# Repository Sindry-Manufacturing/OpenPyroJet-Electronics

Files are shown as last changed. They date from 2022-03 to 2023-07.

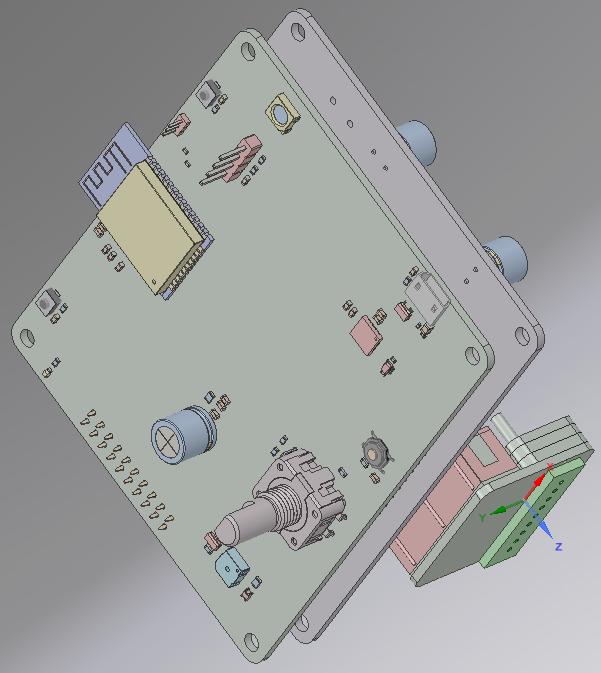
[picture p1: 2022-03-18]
Printhead-Driver/screenshots/3D-PCB-CAD-Model_Controller.jpg

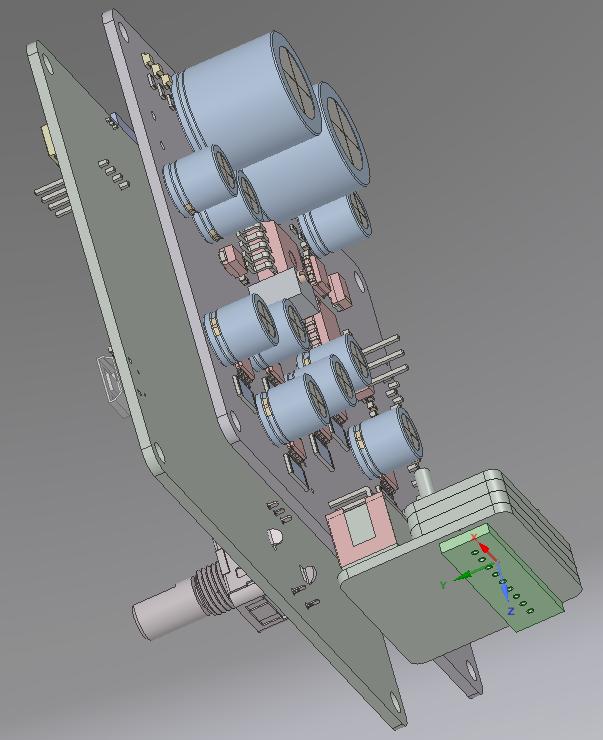
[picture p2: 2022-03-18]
Printhead-Controller/screenshots/3D-PCB-CAD-Model_Driver.jpg

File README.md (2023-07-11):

# OpenPyroJet-Electronics

Software licensed under: AGPL-3

Hardware licensed under: CERN-OHL-S-V2

These sets of sub-folders contain KiCAD 5.1 based designs for experimenting with a PCB based metal/ceramic 3D Printer. 

Gen3.1_Printhead       ; initial experimental PCB based Printhead

Printhead-Controller   ; HW board that runs the Driver board

Printhead-Driver       ; HW circuitry to drive the printhead

software               ; basic Arduino based software to test the Controller & Driver boards.  See: https://github.com/Sindry-Manufacturing/OpenPyrojet-Jetpack  for a much more complete solution

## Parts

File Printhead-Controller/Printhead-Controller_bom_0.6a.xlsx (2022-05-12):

References | Value | Footprint | Quantity Per PCB | Location | LCSC P/N
BZ1 | Buzzer 1KHz - 8KHz | MagneticBuzzer_5.2x5.2_4KHz | 1 | 93-6 | C391030
C2 C3 C5 C6 C7 C8 C9 C10 C12 C14 C15 C18 | 100nF - 6.3V or larger | C_0603_1608Metric | 12 | T15 | C108079
C1 C4 C16 C17 | 10uF - 6.3V or larger | C_0603_1608Metric | 4 | T15 | C326057
C11 | 22uF - 6.3V or larger | C_0603_1608Metric | 1 | T15 | C59461 (https://lcsc.com/product-detail/Multilayer-Ceramic-Capacitors-MLCC-SMD-SMT_Samsung-Electro-Mechanics-CL10A226MQ8NRNC_C59461.html)
C13 - hand solder | 100uF/50V | CP_Radial_D8.0mm_P3.50mm | 1 |  | C365794
D3 | 1N4148 | D_0805_2012Metric | 1 | T9 | C108805
D2 | Green | LED_0603_1608Metric | 1 | T15 | C72043
D4 | PRTR5V0U2X | SOT-143 | 1 | T16 | C316030
D1 | WS2812B | LED_WS2812B_PLCC4_5.0x5.0mm_P3.2mm | 1 | 86-38 | C114586
F1 | 2A Polyfuse | C_0805_2012Metric | 1 | T8 | C2680543 (https://lcsc.com/product-detail/Resettable-Fuses_Jinrui-Electronic-Materials-Co-JK-SMD-0805-200L_C2680543.html)
FB1 | 1uH | R_0805_2012Metric | 1 | T15 | C281114
J5 - hand solder | Conn_02x12_Odd_Even | PinHeader_2x12_P2.54mm_Vertical - Female | 1 | Tray | N/A | https://www.aliexpress.com/item/32747224548.html
J2 | Plug | Hirose_DF13C_CL535-0403-5-51_1x03-1MP_P1.25mm_Vertical | 1 | Tray | N/A* | https://www.aliexpress.com/wholesale?catId=0&initiative_id=SB_20220511181454&SearchText=DF13C-3p+connector
J6 | USB_B_Micro | USB_Micro-B_C319160 | 1 | Table | C319160
Q1 | AO3400A | SOT-23 | 1 | T9 | C344010
R8 | 10 | R_0805_2012Metric | 1 | T2? | C17415
R11 | 47 | R_0603_1608Metric | 1 | T1 | C1211 (https://lcsc.com/product-detail/Chip-span-style-background-color-ff0-Resistor-span-Surface-Mount_UNI-ROYAL-Uniroyal-Elec-0603WAJ0470T5E_C1211.html)
R6 | 2K | R_0603_1608Metric | 1 | T1 | C22975 (https://lcsc.com/product-detail/Chip-span-style-background-color-ff0-Resistor-span-Surface-Mount_UNI-ROYAL-Uniroyal-Elec-0603WAF2001T5E_C22975.html)
R9 R10 | 4.7K | R_0603_1608Metric | 2 | T1 | C23162 (https://lcsc.com/product-detail/Chip-span-style-background-color-ff0-Resistor-span-Surface-Mount_UNI-ROYAL-Uniroyal-Elec-0603WAF4701T5E_C23162.html)
R1 R2 R3 R4 R5 R7 R12 R15 R17 | 10K | R_0603_1608Metric | 9 | T1 | C25804 (https://lcsc.com/product-detail/Chip-span-style-background-color-ff0-Resistor-span-Surface-Mount_UNI-ROYAL-Uniroyal-Elec-0603WAF1002T5E_C25804.html)
R14 | 24K | R_0603_1608Metric | 1 | T1 | C352343 (https://lcsc.com/product-detail/Chip-Resistor-Surface-Mount_Resistor-Today-AECR0603F24K0K9_C352343.html)
R13 | 47K | R_0603_1608Metric | 1 | T1 | C365432 (https://lcsc.com/product-detail/Chip-Resistor-Surface-Mount_Resistor-Today-ETCR0603F47K0K9_C365432.html)
R16 | 1M | R_0603_1608Metric | 1 | T1 | C177633
SW3 | BOOT | SMD_Switch_5x3 | 1 | table | C843665
SW4 | RESET | SMD_Switch_5x3 | 1 | Table | C843665
SW1 | Rotary_Encoder | RotaryEncoder_Alps_EC11E-Switch_Vertical_H20mm | 1 | 93-10 | N/A | https://www.aliexpress.com/item/1744383771.html
SW2 | USER1 | SW_SMD_SPST_SKQG_WithStem_6x6.5 | 1 | table | C318886
U2 | CP2102N-A01-GQFN28 | QFN-28-1EP_5x5mm_P0.5mm_EP3.35x3.35mm | 1 | T12/86-4 | C964632 | not currently in stock, so using an updated one, but very expensive
U3 | DMMT3904W | SOT-363_SC-70-6 | 1 | T7 | C155305
U1 | ESP32-WROOM-32D/E | ESP32-WROOM-32 | 1 | 88-70 | C529581 (https://lcsc.com/product-detail/WiFi-Modules_Espressif-Systems-ESP32-WROOM-32-16MB_C529581.html) | 16MB will allow larger partition size for data collection
Component Groups: | 33
Total components: | 56
Schematic Version: | 0.6a
Schematic Date: | 2022-05-09
BoM Date: | 2022-05-11 17:41
Schematic Source: | Printhead-Controller.sch
 | * | fit the DFN13C vertical/horizontal connector OR 3 pin header.

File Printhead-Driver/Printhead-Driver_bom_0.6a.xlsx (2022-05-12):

References | Value | Footprint | Quantity Per PCB | Location | LCSC P/N
C60 | 470pF | C_0603_1608Metric | 1 | 92-2 | C107092
C3 C4 C7 C11 C12 C15 C16 C19 C20 C23 C24 C27 C28 C31 C32 C34 C36 C37 C51 C53 C55 C65 C67 | 100nF | C_0603_1608Metric | 23 | T15 | C108079 | 6.3V or higher
C33 C35 C68 | 1uF | C_0603_1608Metric | 3 | T15 | C69335
C52 C54 C56 C66 | 10uF | C_0603_1608Metric | 4 | T15 | C326057
C63 | 22uF | C_0603_1608Metric | 1 | T15 | C59461 (https://lcsc.com/product-detail/Multilayer-Ceramic-Capacitors-MLCC-SMD-SMT_Samsung-Electro-Mechanics-CL10A226MQ8NRNC_C59461.html)
C43 | 1000uF/63V | CP_Radial_D16.0mm_P7.50mm | 1 | 96-28 | C10744
C61 C62 | 100nF 10V | C_0603_1608Metric | 2 | T15 | C108079
C8 | 100nF-DNF | C_0603_1608Metric | 1 | T15 | C108079
C41 C42 | 100nF/100V | C_0603_1608Metric | 2 | 92-2 | C113803
C59 | 100nF/35V | C_1206_3216Metric | 1 | 92-2 | C113803
C1 C2 C9 C10 C17 C18 C25 C26 C39 C40 C57 C64 | 100uF/63V | CP_Radial_D8.0mm_P3.50mm | 12 | 96-20 | C365794
C5 C13 C14 C21 C22 C29 C30 | 1nF** | C_0603_1608Metric | 7 |  | C100040 | Just a guestimate. Final value needs testing
C6 | 1nF**DNF | C_0603_1608Metric | 1 |  | C100040 | Just a guestimate. Final value needs testing
C38 C44 C45 C46 C47 C48 C49 C50 | 1nF/DNF | C_0603_1608Metric | 8 |  | C100040 | Just a guestimate. Final value needs testing
C58 | 22uF/35V | C_1210_3225Metric | 1 |  | C2891987 (https://lcsc.com/product-detail/Multilayer-Ceramic-Capacitors-MLCC-SMD-SMT_SANYEAR-C1210X5R226M350NT_C2891987.html)
D3 | 12V-Zener_Diode | D_0805_2012Metric | 1 |  | C21567
D4 D5 D6 D7 | Green | D_0603_1608Metric | 4 | T15 | C142303
D2 | SS34 | D_SMA | 1 | T6 | C8678 (https://lcsc.com/product-detail/Pre-ordered-Products_MDD-Microdiode-Electronics-SS34_C8678.html)
D1 | SS510 | D_SMA | 1 | 91-31 | C65010
F1 | 5A | Fuse_Holder_1808_10.0mmx5mm | 1 | Fuse Tray | C206917 (https://lcsc.com/product-detail/Fuses_Littelfuse-0154005-DRT_C206917.html)
J3 | 24V Power In | JST-XH-2P_SMD | 1 | tray | C64520 (https://lcsc.com/product-detail/Wire-To-Board-Wire-To-Wire-span-style-background-color-ff0-Connector-span_BOOMELE-Boom-Precision-Elec-XH-2PWB_C64520.html)
J2 - hand solder | Controller | PinHeader_2x12_P2.54mm_Vertical | 1 |  |  | can use normal Pinheader parts
J1 - hand solder | IDC_Connector | IDC-Header_2x08_P2.54mm_Horizontal | 1 |  |  | can use normal Pinheader parts
L1 L4 | 1uH 1.4A | L_0805_2012Metric | 2 |  | C281114
L3 | 1uH 4A | L_1uH 4A or more | 1 |  | C2929426 (https://lcsc.com/product-detail/Inductors-SMD_SHOU-HAN-CY54-1-0UH_C2929426.html)
L6 | 1uH/1.4A | L_0805_2012Metric | 1 |  | C281114
L5 | 220uH/2.1A | L_220uH_2A_15x15mm_H8mm | 1 | 96-11 | C970547
L2 | 47uH/5A | L_47uH_4A_11mmx10mm_H4.8mm | 1 | 96-13 | C2847567
Q1 | RU30L30 | PDFN3333 | 1 | 88-22 | C128588
R15 | 1.3K | R_0603_1608Metric | 1 | Book | C22767 (https://lcsc.com/product-detail/Chip-span-style-background-color-ff0-Resistor-span-Surface-Mount_UNI-ROYAL-Uniroyal-Elec-0603WAF1301T5E_C22767.html)
R19 | 2.7K | R_0603_1608Metric | 1 | T1 | C13167 (https://lcsc.com/product-detail/Chip-span-style-background-color-ff0-Resistor-span-Surface-Mount_UNI-ROYAL-Uniroyal-Elec-0603WAF2701T5E_C13167.html)
R14 R18 | 4.7K | R_0603_1608Metric | 2 | T1 | C23162 (https://lcsc.com/product-detail/Chip-span-style-background-color-ff0-Resistor-span-Surface-Mount_UNI-ROYAL-Uniroyal-Elec-0603WAF4701T5E_C23162.html)
R11 | 10K (12K) | R_0603_1608Metric | 1 | T1 | C25804 (https://lcsc.com/product-detail/Chip-span-style-background-color-ff0-Resistor-span-Surface-Mount_UNI-ROYAL-Uniroyal-Elec-0603WAF1002T5E_C25804.html) | Use 10K instead of 12K
R16 | 27K | R_0603_1608Metric | 1 | Book | C22967 (https://lcsc.com/product-detail/Chip-span-style-background-color-ff0-Resistor-span-Surface-Mount_UNI-ROYAL-Uniroyal-Elec-0603WAF2702T5E_C22967.html)
R17 | 62K | R_0603_1608Metric | 1 | Book | C23221 (https://lcsc.com/product-detail/Chip-span-style-background-color-ff0-Resistor-span-Surface-Mount_UNI-ROYAL-Uniroyal-Elec-0603WAF6202T5E_C23221.html)
R9 | 100K (88K) | R_0603_1608Metric | 1 | T1 | C25803 (https://lcsc.com/product-detail/Chip-span-style-background-color-ff0-Resistor-span-Surface-Mount_UNI-ROYAL-Uniroyal-Elec-0603WAF1003T5E_C25803.html) | Use 100K instead of 88K
R20 | 100k | R_0603_1608Metric | 1 | T1 | C25803 (https://lcsc.com/product-detail/Chip-span-style-background-color-ff0-Resistor-span-Surface-Mount_UNI-ROYAL-Uniroyal-Elec-0603WAF1003T5E_C25803.html)
R1 R2 R3 R4 R5 R6 R7 R8 | 0.03R** | R_1206_3216Metric | 8 | T17 | C2903497 | might need to be: .02, .03, .04 or .05 ohms? Depends on PH nozzle resistance
R10 R12 | 10K-DNF | R_0603_1608Metric | 2 | T1 | C25804 (https://lcsc.com/product-detail/Chip-span-style-background-color-ff0-Resistor-span-Surface-Mount_UNI-ROYAL-Uniroyal-Elec-0603WAF1002T5E_C25804.html)
R13 | R0.33 | R_1206_3216Metric | 1 | T17 | C2932844 (https://lcsc.com/product-detail/Chip-span-style-background-color-ff0-Resistor-span-Surface-Mount_Milliohm-HoYH1206-1W-330mR-1_C2932844.html)
RV1 | 100K | Potentiometer_Bourns_3266Y_Vertical | 1 | 96-21 | C118963
U17 | ADC128S102CIMTX | TSSOP-16_4.4x5mm_P0.65mm | 1 |  | C179666
U18 | HE6550MPR | SOT-89-3 | 1 |  | C711959
U3 U7 U8 U11 U12 U15 U16 | INA180A2IDBVR | SOT-23-5 | 7 |  | C192764
U4 | INA180A2IDBVR-DNF | SOT-23-5 | 1 |  | C192764
U19 | MC34063AD | SOIC-8_3.9x4.9mm_P1.27mm | 1 | 96-11 | C32078
U1 U2 U5 U6 U9 U10 U13 U14 | TMI8870B | HSOP-8-1EP_3.9x4.9mm_P1.27mm_EP2.41x3.1mm_ThermalVias | 8 | 96-15 | C2889167
U20 | XC6227C331MR | SOT-23-5 | 1 |  | C216640
VR1 | XL6019 | DPAK170P1435X465-6N | 1 | 88-38/ 96-13 | C73018
Component Groups: | 49
Total components: | 128
Schematic Version: | 0.6a
Schematic Date: | 2022-05-11
BoM Date: | 2022-05-11 17:40
Schematic Source: | Printhead-Driver.sch

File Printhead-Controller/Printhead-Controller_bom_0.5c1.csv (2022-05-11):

References | Value | Footprint | Quantity Per PCB | Location
BZ1 | Buzzer 1KHz - 8KHz | MagneticBuzzer_5.2x5.2_4KHz | 1 | 93-6
C2 C3 C5 C6 C7 C8 C9 C10 C12 C14 C15 C18 | 100nF | C_0603_1608Metric | 12 | T15
C1 C4 C16 C17 | 10uF | C_0603_1608Metric | 4 | T15
C11 | 22uF | C_0603_1608Metric | 1 | T15
C13 | 100uF/50V | CP_Radial_D8.0mm_P3.50mm | 1
D3 | 1N4148 | D_0805_2012Metric | 1 | T9
D2 | Green | LED_0603_1608Metric | 1 | T15
D4 | PRTR5V0U2X | SOT-143 | 1
D1 | WS2812B | LED_WS2812B_PLCC4_5.0x5.0mm_P3.2mm | 1 | 86-38
F1 | 2A Polyfuse | C_0805_2012Metric | 1 | T8
FB1 | 1uH | R_0805_2012Metric | 1 | T15
J4 | USB_B_Micro | USB_Micro-B_C319160 | 1 | Table
JP1 JP2 | Jumper_NC_Small | R_0402_1005Metric | 2 | 87-2?
Q1 | AO3400A | SOT-23 | 1 | T9
R8 | 10 | R_0805_2012Metric | 1 | T2?
R11 | 47 | R_0603_1608Metric | 1 | T1
R6 | 2K | R_0603_1608Metric | 1 | T1
R9 R10 | 4.7K | R_0603_1608Metric | 2 | T1
R1 R2 R3 R4 R5 R7 R12 | 10K | R_0603_1608Metric | 7 | T1
R15 R17 | 12K | R_0402_1005Metric | 2 | 87-2
R14 | 24K | R_0402_1005Metric | 1 | 87-2
R13 | 47K | R_0402_1005Metric | 1 | 87-2
R16 | 1M | R_0603_1608Metric | 1 | T1
SW3 | BOOT | SMD_Switch_5x3 | 1 | table
SW4 | RESET | SMD_Switch_5x3 | 1 | Table
SW1 | Rotary_Encoder | RotaryEncoder_Alps_EC11E-Switch_Vertical_H20mm | 1 | 93-10
SW2 | USER1 | SW_SMD_SPST_SKQG_WithStem_6x6.5 | 1 | table
U2 | CP2102N-A01-GQFN28 | QFN-28-1EP_5x5mm_P0.5mm_EP3.35x3.35mm | 1 | T12/86-4
U3 | DMMT3904W | SOT-363_SC-70-6 | 1 | T7
U1 | ESP32-WROOM-32D | ESP32-WROOM-32 | 1 | 88-70
Component Groups: | 33
Component Count: | 56
Schematic Version: | 0.5c1
Schematic Date: | 16/03/2022
BoM Date: | 18/03/2022 13:29
Schematic Source: | Printhead-Controller.sch

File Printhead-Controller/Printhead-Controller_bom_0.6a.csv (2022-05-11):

Component | Description | Part | References | Value | Footprint | Quantity Per PCB | Datasheet
1 | 4KHz Buzzer 5mmx5mm | Buzzer_3pin | BZ1 | Buzzer 1KHz - 8KHz | MagneticBuzzer_5.2x5.2_4KHz | 1
2 | Unpolarized capacitor, small symbol | C_Small | C2 C3 C5 C6 C7 C8 C9 C10 C12 C14 C15 C18 | 100nF | C_0603_1608Metric | 12 | ~
3 | Unpolarized capacitor, small symbol | C_Small | C1 C4 C16 C17 | 10uF | C_0603_1608Metric | 4 | ~
4 | Unpolarized capacitor, small symbol | C_Small | C11 | 22uF | C_0603_1608Metric | 1 | ~
5 | Polarized capacitor, small symbol | CP_Small | C13 | 100uF/50V | CP_Radial_D8.0mm_P3.50mm | 1 | ~
6 | Diode, small symbol | D_Small | D3 | 1N4148 | D_0805_2012Metric | 1 | ~
7 | Light emitting diode, small symbol | LED_Small | D2 | Green | LED_0603_1608Metric | 1 | ~
8 | Ultra low capacitance double rail-to-rail ESD protection diode, SOT-363 | PRTR5V0U2X | D4 | PRTR5V0U2X | SOT-143 | 1 | https://assets.nexperia.com/documents/data-sheet/PRTR5V0U2X.pdf
9 | RGB LED with integrated controller | WS2812B | D1 | WS2812B | LED_WS2812B_PLCC4_5.0x5.0mm_P3.2mm | 1 | https://cdn-shop.adafruit.com/datasheets/WS2812B.pdf
10 | Resettable fuse, polymeric positive temperature coefficient, small symbol | Polyfuse_Small | F1 | 2A Polyfuse | C_0805_2012Metric | 1 | ~
11 | Ferrite bead, small symbol | Ferrite_Bead_Small | FB1 | 1uH | R_0805_2012Metric | 1 | ~
12 | Generic connector, double row, 02x12, odd/even pin numbering scheme (row 1 odd numbers, row 2 even numbers), script generated (kicad-library-utils/schlib/autogen/connector/) | Conn_02x12_Odd_Even | J5 | Conn_02x12_Odd_Even | PinHeader_2x12_P2.54mm_Vertical | 1 | ~
13 | Generic connector, single row, 01x03, script generated (kicad-library-utils/schlib/autogen/connector/) | Conn_01x03_Male | J3 | Header | PinHeader_1x03_P2.54mm_Vertical | 1 | ~
14 | Generic connector, single row, 01x04, script generated (kicad-library-utils/schlib/autogen/connector/) | Conn_01x04_Male | J4 | OLED Screen | PinHeader_1x04_P2.54mm_Vertical | 1 | ~
15 | Generic connector, single row, 01x03, script generated (kicad-library-utils/schlib/autogen/connector/) | Conn_01x03_Male | J2 | Plug | Hirose_DF13C_CL535-0403-5-51_1x03-1MP_P1.25mm_Vertical | 1 | ~
16 | Generic connector, single row, 01x03, script generated (kicad-library-utils/schlib/autogen/connector/) | Conn_01x03_Male | J1 | Serial Prog | PinHeader_1x03_P1.27mm_Vertical | 1 | ~
17 | USB Micro Type B connector | USB_B_Micro | J6 | USB_B_Micro | USB_Micro-B_C319160 | 1 | ~
18 | 30V Vds, 5.7A Id, N-Channel MOSFET, SOT-23 | AO3400A | Q1 | AO3400A | SOT-23 | 1 | http://www.aosmd.com/pdfs/datasheet/AO3400A.pdf
19 | Resistor, small symbol | R_Small | R8 | 10 | R_0805_2012Metric | 1 | ~
20 | Resistor, small symbol | R_Small | R11 | 47 | R_0603_1608Metric | 1 | ~
21 | Resistor, small symbol | R_Small | R6 | 2K | R_0603_1608Metric | 1 | ~
22 | Resistor, small symbol | R_Small | R9 R10 | 4.7K | R_0603_1608Metric | 2 | ~
23 | Resistor, small symbol | R_Small | R1 R2 R3 R4 R5 R7 R12 R15 R17 | 10K | R_0603_1608Metric | 9 | ~
24 | Resistor, small symbol | R_Small | R14 | 24K | R_0603_1608Metric | 1 | ~
25 | Resistor, small symbol | R_Small | R13 | 47K | R_0603_1608Metric | 1 | ~
26 | Resistor, small symbol | R_Small | R16 | 1M | R_0603_1608Metric | 1 | ~
27 | Push button switch, generic, two pins | SW_Push | SW3 | BOOT | SMD_Switch_5x3 | 1 | ~
28 | Push button switch, generic, two pins | SW_Push | SW4 | RESET | SMD_Switch_5x3 | 1 | ~
29 | Rotary encoder, dual channel, incremental quadrate outputs, with switch | Rotary_Encoder_Switch | SW1 | Rotary_Encoder | RotaryEncoder_Alps_EC11E-Switch_Vertical_H20mm | 1 | ~
30 | Push button switch, generic, two pins | SW_Push | SW2 | USER1 | SW_SMD_SPST_SKQG_WithStem_6x6.5 | 1 | ~
31 | USB to UART master bridge, QFN-28 | CP2102N-A01-GQFN28 | U2 | CP2102N-A01-GQFN28 | QFN-28-1EP_5x5mm_P0.5mm_EP3.35x3.35mm | 1 | https://www.silabs.com/documents/public/data-sheets/cp2102n-datasheet.pdf
32 | Dual NPN Transistors, 40V 200mA, 300MHz | DMMT3904W | U3 | DMMT3904W | SOT-363_SC-70-6 | 1
33 | RF Module, ESP32-D0WD SoC, Wi-Fi 802.11b/g/n, Bluetooth, BLE, 32-bit, 2.7-3.6V, onboard antenna, SMD | ESP32-WROOM-32D | U1 | ESP32-WROOM-32D | ESP32-WROOM-32 | 1 | https://www.espressif.com/sites/default/files/documentation/esp32-wroom-32d_esp32-wroom-32u_datasheet_en.pdf
Component Groups: | 33
Component Count: | 56
Fitted Components: | 56
Number of PCBs: | 1
Total components: | 56
Schematic Version: | 0.6a
Schematic Date: | 2022-05-09
PCB Variant: | udefault
BoM Date: | 11/05/2022 17:41:04
Schematic Source: | Printhead-Controller.sch
KiCad Version: | Eeschema (5.1.12)-1

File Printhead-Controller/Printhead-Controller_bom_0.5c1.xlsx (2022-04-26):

References | Value | Footprint | Quantity Per PCB | Location | LCSC P/N | Notes
BZ1 | Buzzer 1KHz - 8KHz | MagneticBuzzer_5.2x5.2_4KHz | 1 | 93-6 | C391030
C2 C3 C5 C6 C7 C8 C9 C10 C12 C14 C15 C18 | 100nF | C_0603_1608Metric | 12 | T15 | C108079
C1 C4 C16 C17 | 10uF | C_0603_1608Metric | 4 | T15 | C326057
C11 | 22uF | C_0603_1608Metric | 1 | T15 | C59461 (https://lcsc.com/product-detail/Multilayer-Ceramic-Capacitors-MLCC-SMD-SMT_Samsung-Electro-Mechanics-CL10A226MQ8NRNC_C59461.html)
C13 | 100uF/50V | CP_Radial_D8.0mm_P3.50mm | 1 |  | C365794
D3 | 1N4148 | D_0805_2012Metric | 1 | T9 | C108805 | I think this will fit a 0805
D2 | Green | LED_0603_1608Metric | 1 | T15 | C72043
D4 | PRTR5V0U2X | SOT-143 | 1 | T16 | C316030
D1 | WS2812B | LED_WS2812B_PLCC4_5.0x5.0mm_P3.2mm | 1 | 86-38 | C114586
F1 | 2A Polyfuse | C_0805_2012Metric | 1 | T8 | C2680543 (https://lcsc.com/product-detail/Resettable-Fuses_Jinrui-Electronic-Materials-Co-JK-SMD-0805-200L_C2680543.html)
FB1 | 1uH | R_0805_2012Metric | 1 | T15 | C281114 | or use C79382 ferrite bead
J4 | USB_B_Micro | USB_Micro-B_C319160 | 1 | Table | C319160
JP1 JP2 | Jumper_NC_Small | R_0402_1005Metric | 2 | 87-2? | C106231 | or just use a solder+wire
Q1 | AO3400A | SOT-23 | 1 | T9 | C344010
R8 | 10 | R_0805_2012Metric | 1 | T2? | C17415
R11 | 47 | R_0603_1608Metric | 1 | T1 | C1211 (https://lcsc.com/product-detail/Chip-span-style-background-color-ff0-Resistor-span-Surface-Mount_UNI-ROYAL-Uniroyal-Elec-0603WAJ0470T5E_C1211.html)
R6 | 2K | R_0603_1608Metric | 1 | T1 | C22975 (https://lcsc.com/product-detail/Chip-span-style-background-color-ff0-Resistor-span-Surface-Mount_UNI-ROYAL-Uniroyal-Elec-0603WAF2001T5E_C22975.html)
R9 R10 | 4.7K | R_0603_1608Metric | 2 | T1 | C23162 (https://lcsc.com/product-detail/Chip-span-style-background-color-ff0-Resistor-span-Surface-Mount_UNI-ROYAL-Uniroyal-Elec-0603WAF4701T5E_C23162.html)
R1 R2 R3 R4 R5 R7 R12 | 10K | R_0603_1608Metric | 7 | T1 | C25804 (https://lcsc.com/product-detail/Chip-span-style-background-color-ff0-Resistor-span-Surface-Mount_UNI-ROYAL-Uniroyal-Elec-0603WAF1002T5E_C25804.html)
R15 R17 | 12K | R_0402_1005Metric | 2 | 87-2 | C25752
R14 | 24K | R_0402_1005Metric | 1 | 87-2 | C138026
R13 | 47K | R_0402_1005Metric | 1 | 87-2 | C93943
R16 | 1M | R_0603_1608Metric | 1 | T1 | C177633
SW3 | BOOT | SMD_Switch_5x3 | 1 | table | C843665
SW4 | RESET | SMD_Switch_5x3 | 1 | Table | C843665
SW1 | Rotary_Encoder | RotaryEncoder_Alps_EC11E-Switch_Vertical_H20mm | 1 | 93-10 | N/A | https://www.aliexpress.com/item/1744383771.html
SW2 | USER1 | SW_SMD_SPST_SKQG_WithStem_6x6.5 | 1 | table | C318886
U2 | CP2102N-A01-GQFN28 | QFN-28-1EP_5x5mm_P0.5mm_EP3.35x3.35mm | 1 | T12/86-4 | C964632 | not currently in stock, so using an updated one, but very expensive
U3 | DMMT3904W | SOT-363_SC-70-6 | 1 | T7 | C155305
U1 | ESP32-WROOM-32E/16MB | ESP32-WROOM-32 | 1 | 88-70 | C529581 (https://lcsc.com/product-detail/WiFi-Modules_Espressif-Systems-ESP32-WROOM-32-16MB_C529581.html) | 16MB will allow larger partition size for data collection
Component Groups: | 33
Component Count: | 56
Schematic Version: | 0.5c1
Schematic Date: | 2022-03-16
BoM Date: | 2022-03-18 13:29
Schematic Source: | Printhead-Controller.sch

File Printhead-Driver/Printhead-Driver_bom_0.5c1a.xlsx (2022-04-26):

References | Value | Footprint | Location | LCSC P/N | Quantity Per PCB | Notes
C40 | 470pF | C_0603_1608Metric | 92-2 | C107092 | 1
C3 C4 C9 C10 C15 C16 C21 C22 C31 C34 C39 C41 | 100nF | C_0603_1608Metric | T15 | C108079 | 20 | 6.3V or higher
C35 | 4.7uF | C_0603_1608Metric | T15 | C69335 | 1
C33 | 10uF | C_0603_1608Metric | T15 | C326057 | 1
C32 C42 | 22uF | C_0603_1608Metric | T15 | C59461 (https://lcsc.com/product-detail/Multilayer-Ceramic-Capacitors-MLCC-SMD-SMT_Samsung-Electro-Mechanics-CL10A226MQ8NRNC_C59461.html) | 2
C29 C30 | 1000uF/63V | CP_Radial_D16.0mm_P7.50mm | 96-28 | C10744 | 2
C44 | 100nF-DNF | C_0603_1608Metric |  | C108079 | 1 | only fit if needed
C28 C19 C20 C13 C14 C7 C8 C1 C2 | 100nF/100V | C_0603_1608Metric | 92-2 | C113803 | 1 | 100V
C27 C38 | 100nF/100V | C_0603_1608Metric | 92-2 | C113803 | 2 | use 100V
C5 C6 C11 C12 C17 C18 C23 C24 C25 C26 C36 C43 | 100uF/63V | CP_Radial_D8.0mm_P3.50mm | 96-20 | C365794 | 12
C37 - DNF (voltage not available in 0603) Order 1206: C342620 for next iteration of PCB | 22uF/50V | C_0603_1608Metric | 96-19 | N/A | 1 | (voltage not available in 0603) Order 1206: C342620 for next iteration of PCB
D2 | 1N4007 | D_SMA |  | C727081 | 1
D4 D5 D6 | Green | LED_0805_2012Metric | T15 | C142303 | 3
D3 | SS34 | D_SMA | T6 | C8678 (https://lcsc.com/product-detail/Pre-ordered-Products_MDD-Microdiode-Electronics-SS34_C8678.html) | 1
D1 | SS510 | D_SMA | 91-31 | C65010 | 1
FB1 - what fits best? Book | 120 m Ohm Ferrite Bead | R_0805_2012Metric | book | C79382 | 1
J2 - DNF | 2 x 10 Pinheader | PinHeader_2x10_P2.54mm_Vertical |  |  | 1 | can use normal Pinheader parts
J3 - hand solder | 24V Power In | TerminalBlock_Altech_AK300-2_P5.00mm | tray | C387831 | 1 | Note: needs testing to make sure footprint is ok
J4 - hand solder | ADC Select1 | PinHeader_1x03_P2.54mm_Vertical |  |  | 1 | can use normal Pinheader parts
J1 - hand solder | IDC_Connector | IDC-Header_2x08_P2.54mm_Horizontal |  |  | 1 | can use normal Pinheader parts
L2 | 220uH/2.1A | L_220uH_2A_15x15mm_H8mm | 96-11 | C970547 | 1
L1 | 47uH/5A | L_47uH_4A_11mmx10mm_H4.8mm | 96-13 | C2847567 | 1
R14 | 1.8K | R_0603_1608Metric | T1 | C4177 (https://lcsc.com/product-detail/Chip-span-style-background-color-ff0-Resistor-span-Surface-Mount_UNI-ROYAL-Uniroyal-Elec-0603WAF1801T5E_C4177.html) | 1
R17 | 2.7K | R_0805_2012Metric | T2 | C17530 (https://lcsc.com/product-detail/Chip-span-style-background-color-ff0-Resistor-span-Surface-Mount_UNI-ROYAL-Uniroyal-Elec-0805W8F2701T5E_C17530.html) | 1 | any value from 2K - 3K is ok
R13 | 3K | R_0603_1608Metric | T1 | C4211 (https://lcsc.com/product-detail/Chip-span-style-background-color-ff0-Resistor-span-Surface-Mount_UNI-ROYAL-Uniroyal-Elec-0603WAF3001T5E_C4211.html) | 1
R9 R10 - DNF | 10K | R_0603_1608Metric | T1 | C25804 (https://lcsc.com/product-detail/Chip-span-style-background-color-ff0-Resistor-span-Surface-Mount_UNI-ROYAL-Uniroyal-Elec-0603WAF1002T5E_C25804.html) | 2 | These are just placeholder footprints for later use
R11 | 10K | R_0603_1608Metric | T1 | C25804 (https://lcsc.com/product-detail/Chip-span-style-background-color-ff0-Resistor-span-Surface-Mount_UNI-ROYAL-Uniroyal-Elec-0603WAF1002T5E_C25804.html) | 1
R15 | 25K | R_0805_2012Metric | book | C153306 (https://lcsc.com/product-detail/Chip-span-style-background-color-ff0-Resistor-span-Surface-Mount_Ever-Ohms-Tech-TR0805B25K0P0525Z_C153306.html) | 1
R16 | 62K | R_0805_2012Metric | book | C17783 (https://lcsc.com/product-detail/Chip-span-style-background-color-ff0-Resistor-span-Surface-Mount_UNI-ROYAL-Uniroyal-Elec-0805W8F6202T5E_C17783.html) | 1
R1 R2 R3 R4 R5 R6 R7 R8 | 0.03R** | R_2512_6332Metric | T4 | C2934377 (https://lcsc.com/product-detail/Chip-span-style-background-color-ff0-Resistor-span-Surface-Mount_FOJAN-FRL2512JR300TS_C2934377.html) | 8 | Needs testing! Might need to be a different value
R12 | R0.33 | R_2512_6332Metric | T4 | C2934378 (https://lcsc.com/product-detail/Chip-span-style-background-color-ff0-Resistor-span-Surface-Mount_FOJAN-FRL2512JR330TS_C2934378.html) | 1 | Needs testing! Might need to be a different value
RV1 | 100K | Potentiometer_Bourns_3266Y_Vertical | 96-21 | C118963 | 1
U11 | ADC121C021CIMM | MSOP-8_3x3mm_P0.65mm | 96-14 | C201638 | 1 | Wrong footprint!!
U10 | MC34063AD | SOIC-8_3.9x4.9mm_P1.27mm | 96-11 | C32078 | 1
U9 | MCA1101-5-3 | SOIC-16W_7.5x10.3mm_P1.27mm | 96-29 | N/A | 1 | Mouser only: P/N: 438-MCA1101-5-3
U1 U2 U3 U4 U5 U6 U7 U8 | TMI8870B | HSOP-8-1EP_3.9x4.9mm_P1.27mm_EP2.41x3.1mm_ThermalVias | 96-15 | C2889167 | 8
VR1 | XL6019 | DPAK170P1435X465-6N | 88-38/ 96-13 | C73018 | 1
Component Groups: | 36
Total components: | 87
Schematic Version: | 0.5c1
Schematic Date: | 2022-03-18
BoM Date: | 2022-03-18 17:04
Schematic Source: | Printhead-Driver.sch

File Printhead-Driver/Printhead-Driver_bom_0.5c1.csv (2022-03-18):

Component | Description | Part | References | Value | Footprint | Quantity Per PCB | Datasheet
1 | Unpolarized capacitor, small symbol | C_Small | C40 | 470pF | C_0603_1608Metric | 1 | ~
2 | Unpolarized capacitor, small symbol | C_Small | C1 C2 C3 C4 C7 C8 C9 C10 C13 C14 C15 C16 C19 C20 C21 C22 C31 C34 C39 C41 | 100nF | C_0603_1608Metric | 20 | ~
3 | Unpolarized capacitor, small symbol | C_Small | C35 | 4.7uF | C_0603_1608Metric | 1 | ~
4 | Unpolarized capacitor, small symbol | C_Small | C33 | 10uF | C_0603_1608Metric | 1 | ~
5 | Unpolarized capacitor, small symbol | C_Small | C32 C42 | 22uF | C_0603_1608Metric | 2 | ~
6 | Polarized capacitor, small symbol | CP_Small | C29 C30 | 1000uF/63V | CP_Radial_D16.0mm_P7.50mm | 2 | ~
7 | Unpolarized capacitor, small symbol | C_Small | C44 | 100nF-DNF | C_0603_1608Metric | 1 | ~
8 | Unpolarized capacitor, small symbol | C_Small | C28 | 100nF/100V | C_0603_1608Metric | 1 | ~
9 | Unpolarized capacitor, small symbol | C_Small | C27 C38 | 100nF/50V | C_0603_1608Metric | 2 | ~
10 | Polarized capacitor, small symbol | CP_Small | C5 C6 C11 C12 C17 C18 C23 C24 C25 C26 C36 C43 | 100uF/63V | CP_Radial_D8.0mm_P3.50mm | 12 | ~
11 | Unpolarized capacitor, small symbol | C_Small | C37 | 22uF/50V | C_0603_1608Metric | 1 | ~
12 | Diode, small symbol | D_Small | D2 | 1N4007 | D_SMA | 1 | ~
13 | Light emitting diode, small symbol | LED_Small | D4 D5 D6 | Green | LED_0805_2012Metric | 3 | ~
14 | Schottky diode, small symbol | D_Schottky_Small | D3 | SS34 | D_SMA | 1 | ~
15 | Schottky diode, small symbol | D_Schottky_Small | D1 | SS510 | D_SMA | 1 | ~
16 | Ferrite bead, small symbol | Ferrite_Bead_Small | FB1 | 120uH | R_0805_2012Metric | 1 | ~
17 | Generic connector, double row, 02x10, odd/even pin numbering scheme (row 1 odd numbers, row 2 even numbers), script generated (kicad-library-utils/schlib/autogen/connector/) | Conn_02x10_Odd_Even | J2 | 2 x 10 Pinheader | PinHeader_2x10_P2.54mm_Vertical | 1 | ~
18 | Generic screw terminal, single row, 01x02, script generated (kicad-library-utils/schlib/autogen/connector/) | Screw_Terminal_01x02 | J3 | 24V Power In | TerminalBlock_Altech_AK300-2_P5.00mm | 1 | ~
19 | Generic connector, single row, 01x03, script generated (kicad-library-utils/schlib/autogen/connector/) | Conn_01x03_Male | J4 | ADC Select1 | PinHeader_1x03_P2.54mm_Vertical | 1 | ~
20 | Generic connector, double row, 02x08, odd/even pin numbering scheme (row 1 odd numbers, row 2 even numbers), script generated (kicad-library-utils/schlib/autogen/connector/) | Conn_02x08_Odd_Even | J1 | IDC_Connector | IDC-Header_2x08_P2.54mm_Horizontal | 1 | ~
21 | Inductor, small symbol | L_Small | L2 | 220uH/2.1A | L_220uH_2A_15x15mm_H8mm | 1 | ~
22 | Inductor, small symbol | L_Small | L1 | 47uH/5A | L_47uH_4A_11mmx10mm_H4.8mm | 1 | ~
23 | Resistor, small symbol | R_Small | R14 | 1.8K | R_0603_1608Metric | 1 | ~
24 | Resistor, small symbol | R_Small | R17 | 2.7K | R_0805_2012Metric | 1 | ~
25 | Resistor, small symbol | R_Small | R13 | 3K | R_0603_1608Metric | 1 | ~
26 | Resistor, small symbol | R_Small | R9 R10 R11 | 10K | R_0603_1608Metric | 3 | ~
27 | Resistor, small symbol | R_Small | R15 | 25K | R_0805_2012Metric | 1 | ~
28 | Resistor, small symbol | R_Small | R16 | 60K | R_0805_2012Metric | 1 | ~
29 | Resistor, small symbol | R_Small | R1 R2 R3 R4 R5 R6 R7 R8 | 0.03R** | R_2512_6332Metric | 8 | ~
30 | Resistor, small symbol | R_Small | R12 | R0.33 | R_2512_6332Metric | 1 | ~
31 | Potentiometer | R_POT | RV1 | 100K | Potentiometer_Bourns_3266Y_Vertical | 1 | ~
32 | I2C-Compatible, 12-Bit Analog-to-Digital Converter with Alert Function, MSOP-8 | ADC121C021CIMM | U11 | ADC121C021CIMM | MSOP-8_3x3mm_P0.65mm | 1 | http://www.ti.com/lit/ds/symlink/adc121c021.pdf
33 | 1.5A, step-up/down/inverting switching regulator, 3-40V Vin, 100kHz, SO-8 | MC34063AD | U10 | MC34063AD | SOIC-8_3.9x4.9mm_P1.27mm | 1 | http://www.onsemi.com/pub_link/Collateral/MC34063A-D.PDF
34 | Current Sensor, 5A, 1.5MHz | MCA1101-5-3 | U9 | MCA1101-5-3 | SOIC-16W_7.5x10.3mm_P1.27mm | 1
35 | Motor Driver, 45V 3.6A, HSOP-8-1EP | TMI8870B | U1 U2 U3 U4 U5 U6 U7 U8 | TMI8870B | HSOP-8-1EP_3.9x4.9mm_P1.27mm_EP2.41x3.1mm_ThermalVias | 8
36 | DC-DC Buck, Boost 3-40V in, up to 60V out at 4A | XL6019 | VR1 | XL6019 | DPAK170P1435X465-6N | 1
Component Groups: | 36
Component Count: | 87
Fitted Components: | 87
Number of PCBs: | 1
Total components: | 87
Schematic Version: | 0.5c1
Schematic Date: | 2022-03-18
PCB Variant: | default
BoM Date: | 18/03/2022 17:04:29
Schematic Source: | Printhead-Driver.sch
KiCad Version: | Eeschema (5.1.12)-1

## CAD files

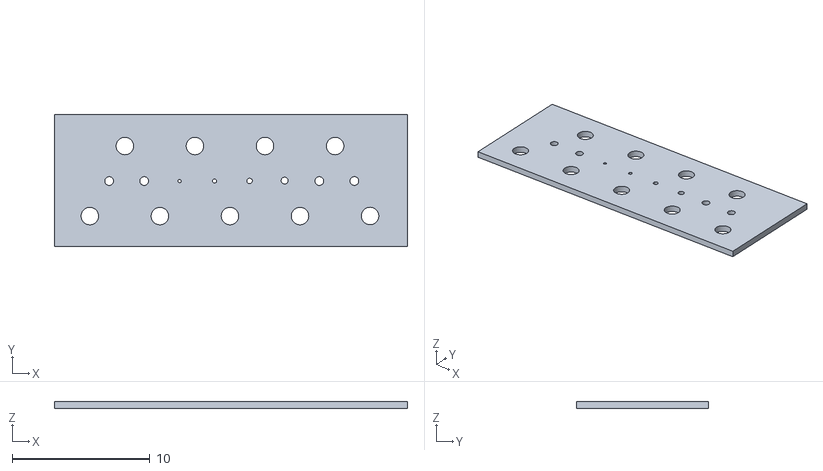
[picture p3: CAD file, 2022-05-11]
Gen3.1_Printhead/CAD/PrintheadV2_Assembly1.10.obj
25.6 x 9.54 x 0.5

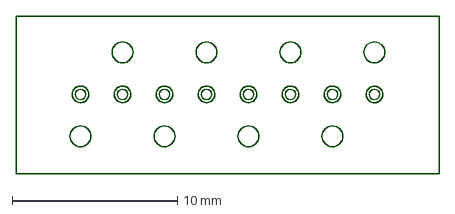
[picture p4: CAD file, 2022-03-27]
Gen3.1_Printhead/Nozzle/PrintheadV2_Assembly1.8-nozzle.dxf
25.6 x 9.54 mm

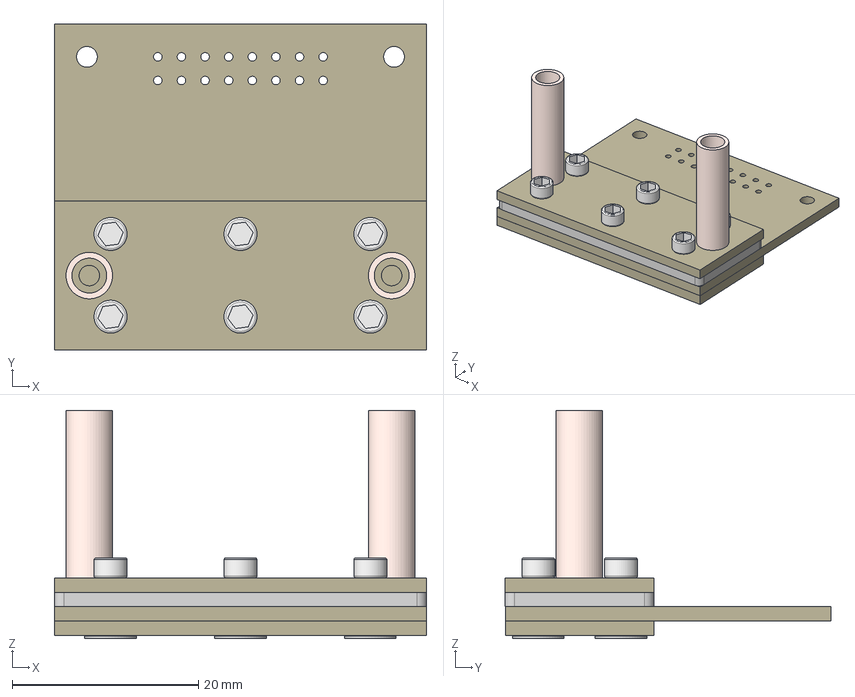
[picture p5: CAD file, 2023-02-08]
Gen4_Printhead/opjpcbprintheadassemblyv5 v14.step
40.0 x 35.1 x 24.5 mm
Board
Board_1
opjtankplatev5
Board_2
zeroheightthreadedinserts x 6
clampingfastenersstainlesssteelscrews x 6
inletoutletpipes x 2
siliconcarbideheaterfilament

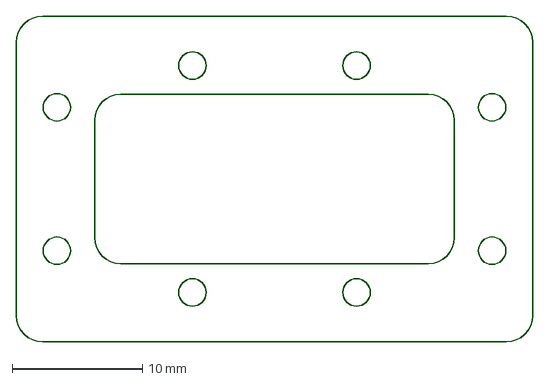
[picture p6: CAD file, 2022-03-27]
Gen3.1_Printhead/Nozzle/PrintheadV2_Assembly1.8-chamber.dxf
39.6 x 25.0 mm

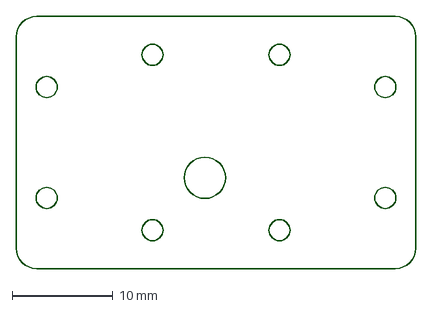
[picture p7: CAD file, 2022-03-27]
Gen3.1_Printhead/Nozzle/PrintheadV2_Assembly1.8-toplate.dxf
39.6 x 25.0 mm

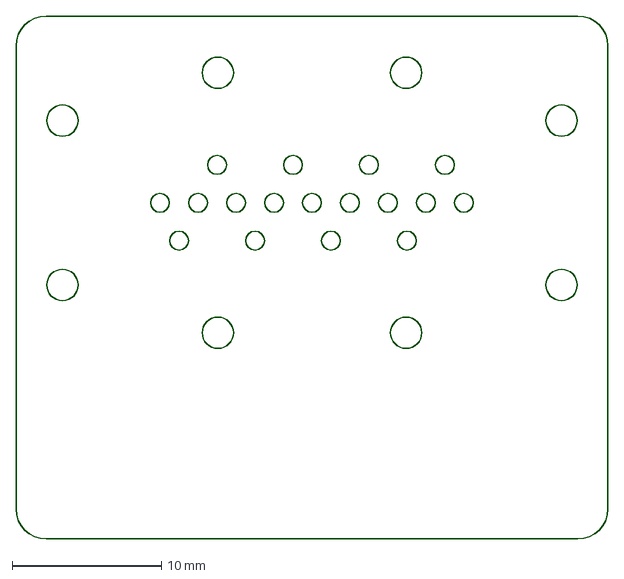
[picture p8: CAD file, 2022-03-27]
Gen3.1_Printhead/Nozzle/PrintheadV2_Assembly1.8-connections.dxf
39.6 x 35.0 mm

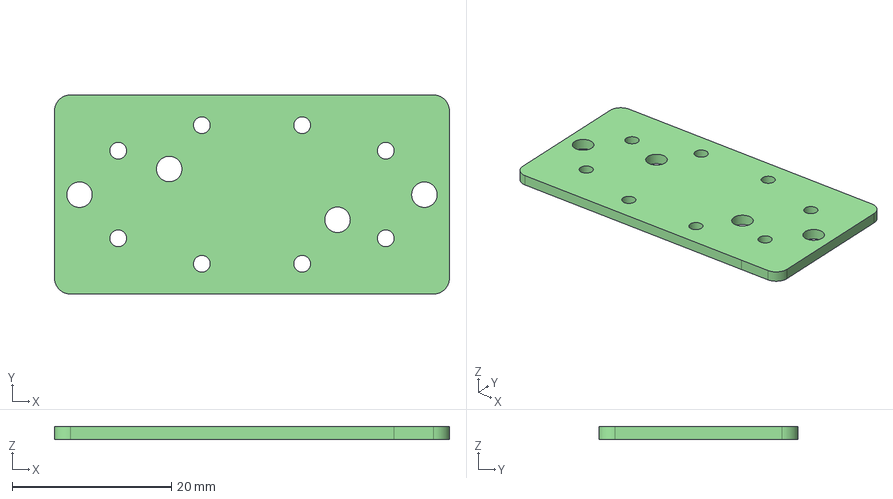
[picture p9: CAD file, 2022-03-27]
Gen3.1_Printhead/Nozzle/manufacture-top/Nozzle-top.step
49.6 x 25.0 x 1.60 mm

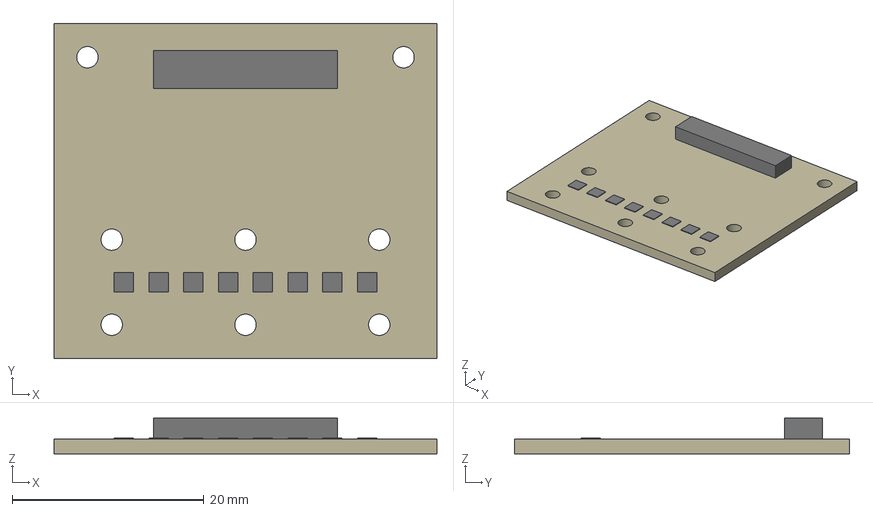
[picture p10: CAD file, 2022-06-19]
Gen4_Printhead/STEPfiles/opjpcbprintheadV5 v3.step
40.0 x 35.0 x 3.74 mm
Board
CON16
OPJGASGUN x 8

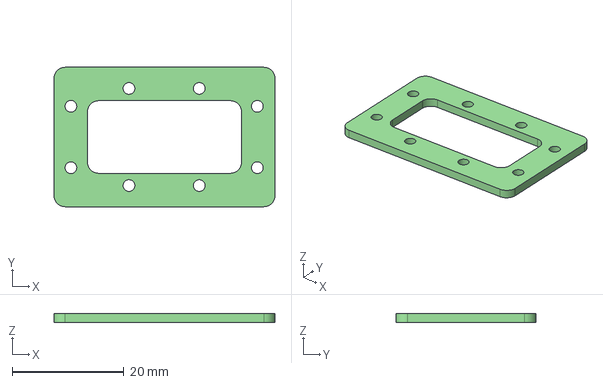
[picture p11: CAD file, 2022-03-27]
Gen3.1_Printhead/CAD/Nozzle-chamber.step
39.6 x 25.0 x 1.60 mm

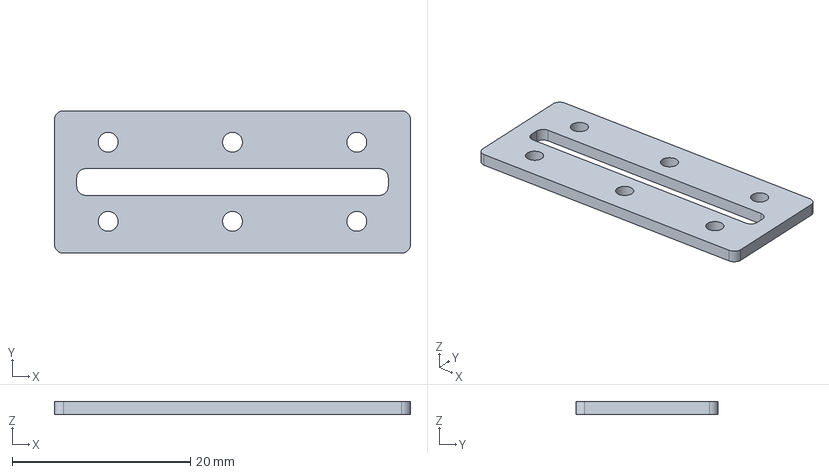
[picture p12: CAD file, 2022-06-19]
Gen4_Printhead/STEPfiles/opjtankplatev5 v1.step
40.0 x 16.0 x 1.50 mm
Board
Packages
1-copper
16-copper
1-soldermask
16-soldermask

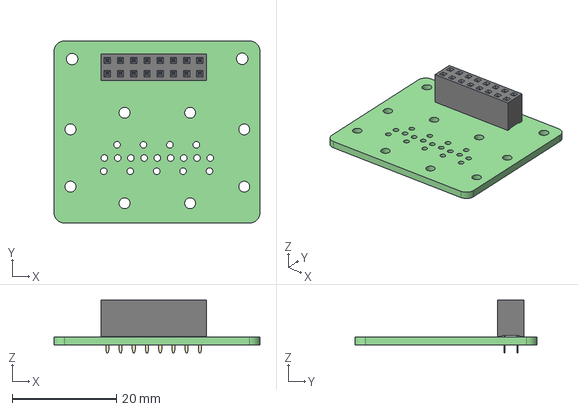
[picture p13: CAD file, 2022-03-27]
Gen3.1_Printhead/CAD/Nozzle-connector.step
39.6 x 35.0 x 10.1 mm

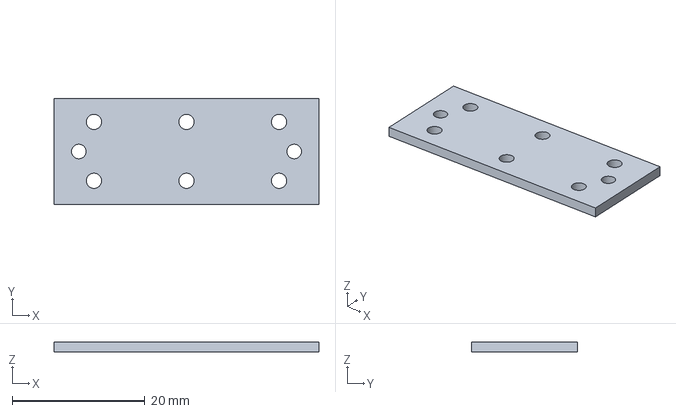
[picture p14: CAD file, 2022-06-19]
Gen4_Printhead/STEPfiles/opjinletplatev5 v3.step
40.0 x 16.0 x 1.57 mm

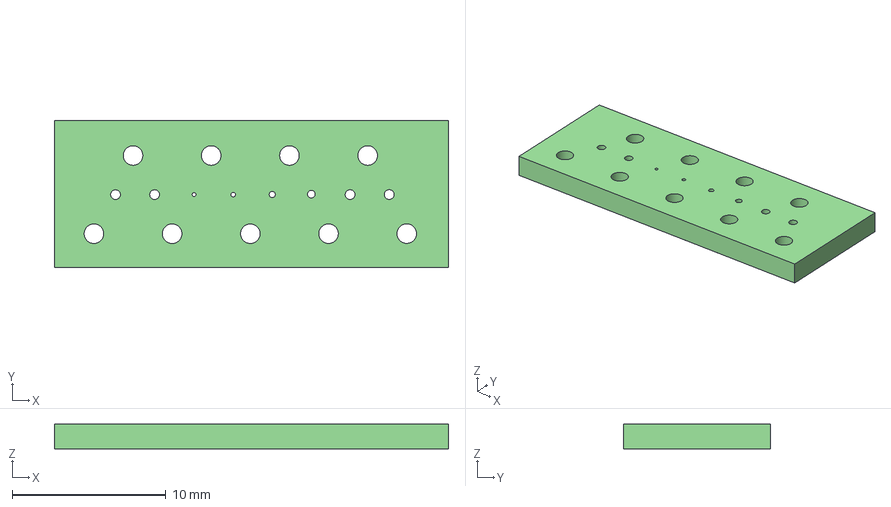
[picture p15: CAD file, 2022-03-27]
Gen3.1_Printhead/CAD/Nozzle-nozzle.step
25.6 x 9.54 x 1.60 mm

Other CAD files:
Gen4_Printhead/STEPfiles/opjpcbnozzleplatev6 v2.step
Gen3.1_Printhead/CAD/Nozzle-top.step
Gen4_Printhead/dxffiles/opjinletplatev5 v3.dxf
Gen4_Printhead/dxffiles/opjpcbnozzleplatev6 v2.dxf
Gen4_Printhead/dxffiles/opjpcbprintheadV5 v3.dxf
Gen4_Printhead/dxffiles/opjtankplatev5 v1.dxf
Gen4_Printhead/opjpcbprintheadassemblyv5 v15.f3z

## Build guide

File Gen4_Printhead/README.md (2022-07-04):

Production:
JLPCB, 2 layer, 1.6mm, green, ENIG on connector plate only standard solder finish on all others. 
Connection is provided by a 0.1" 16 pin IDC female box connector.

This is the latest edition of the pyrojet printhead, with straight pass through nozzles, and material feedin channels, as well as a greatly simplified assembly process.
The use of threaded inserts helps greatly with ease of assembly and disassembly, as well as circuit routing. 
The prior generation's M1 screws have been eliminated completely. 
the 16 pin IDC connector has been retained. 
the nozzles have all been made as 0.4 mm diameter through holes with no plating of any kind. The heaters on the connector plate have been made as 0.4mm wide contacts.

The tank has been narrowed to improve fuel circulation speed, and the inlet plate has has the solder pads for the inlet and outlet copper pipes expanded to facilitate easier soldering. 

The threaded inserts that are epoxied into the 6 large holes in the nozzle plate are found here:
https://www.keyelco.com/product.cfm/product_id/14462

The 6 screws that hold the assembly together are #2-56 X 1/4"  standard stainless steel socket cap screws, driven by a 5/64" driver allen key. 
these screws can be found here:
https://www.amazon.com/dp/B073WPSSNS?psc=1&ref=ppx_yo2ov_dt_b_product_details

The zip files herein are the manufacturing files you need to upload at JLPCB or manufacturer of your choice to get your print heads made. 
You can upload them as is and recieve your printheads in a couple weeks. 
Generally, the print heads are cheaper per part in larger batches.

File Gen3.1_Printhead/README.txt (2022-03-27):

Printhead Version Gen3.1:
-------------------------

* Designed in Design Spark Mechanical: https://www.rs-online.com/designspark/mechanical-software and then imported into KiCAD: https://www.kicad.org/ via exported DFX files.

* STEP files are currently more accurate than the CAD design, as things have been further tweaked in KiCAD

* PCB's have been panelised with Gerber Panelizer:  http://www2.thisisnotrocketscience.nl/software/pcb-panelizer/

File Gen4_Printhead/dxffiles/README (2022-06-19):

this is where the 2D CAD files of the gen4 printhead are stored.
Board files, dxfs etc.

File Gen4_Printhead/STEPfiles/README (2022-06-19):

These are the 3D step files and solid models for the gen4 printhead design.

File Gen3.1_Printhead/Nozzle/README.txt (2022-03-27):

This directory contains KiCAD 5.1.x design files for a set of PCB's that make up the OpenPyroJet Gen 3.1 printhead. 
 
The directory could be better named as Printhead (as opposed to Nozzle), but I believe thats hard to do once a KiCAD project has been started?

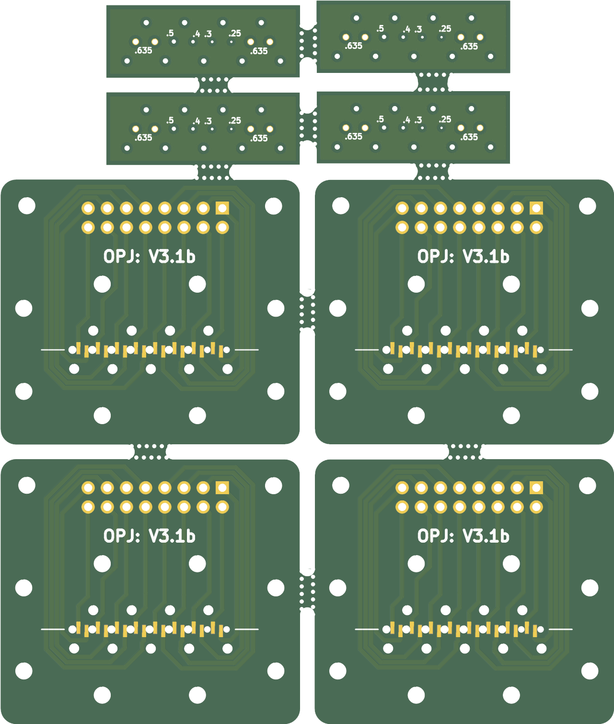
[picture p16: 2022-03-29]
Gen3.1_Printhead/Nozzle/PCB-Panels/Panel-Connector-Nozzles/connector-Nozzle-panel_Combined_Bottom.png

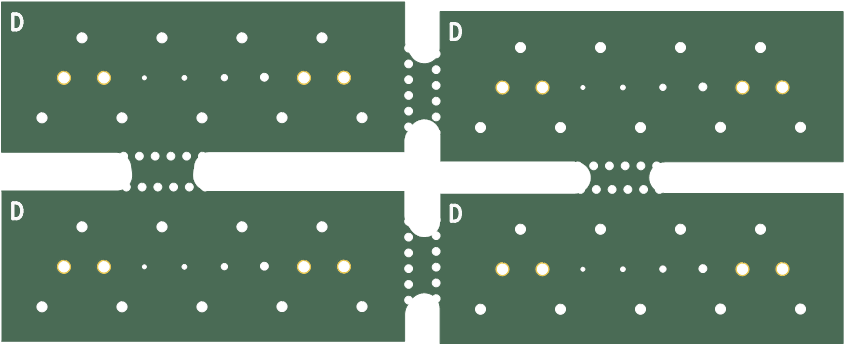
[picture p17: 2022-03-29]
Gen3.1_Printhead/Nozzle/PCB-Panels/Panel-Four-Nozzles/connector-Nozzle-panel_Combined_Top.png

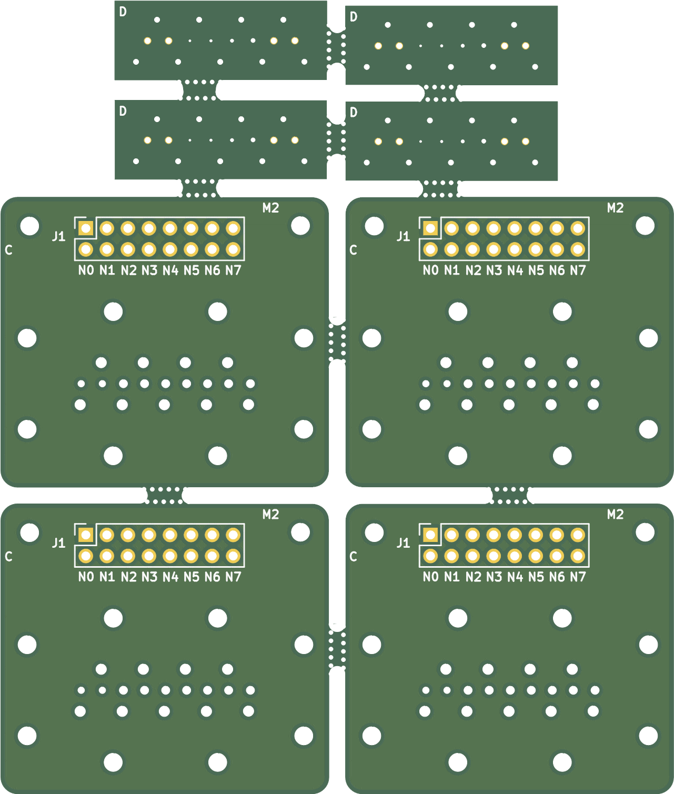
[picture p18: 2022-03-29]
Gen3.1_Printhead/Nozzle/PCB-Panels/Panel-Connector-Nozzles/connector-Nozzle-panel_Combined_Top.png

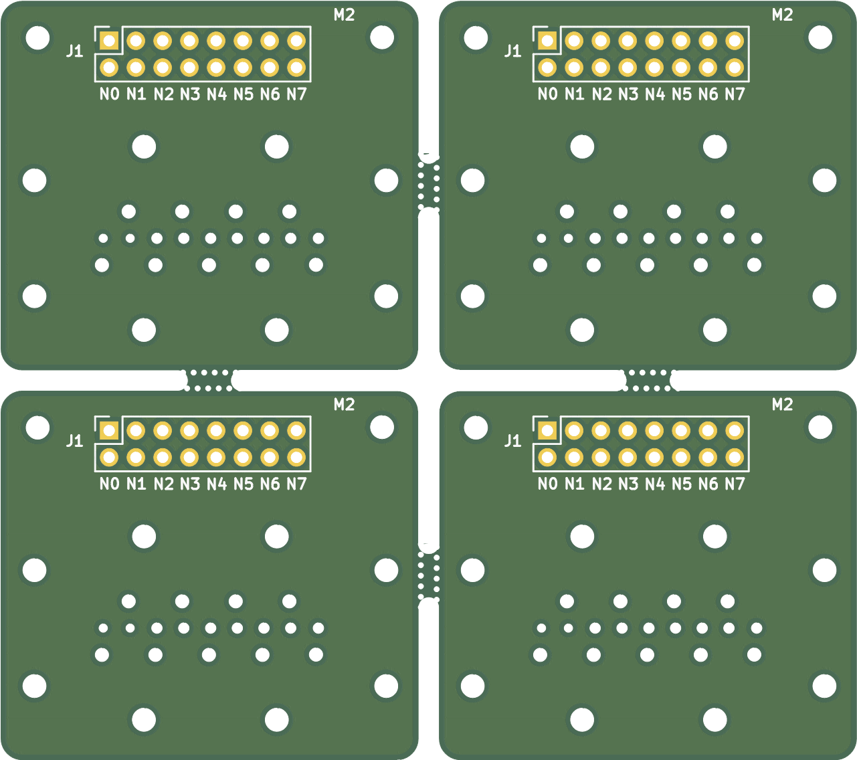
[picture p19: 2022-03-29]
Gen3.1_Printhead/Nozzle/PCB-Panels/Panel-Four-Connectors/connector-panel_Combined_Top.png

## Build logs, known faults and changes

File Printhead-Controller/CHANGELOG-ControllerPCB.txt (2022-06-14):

This directory contains KiCAD 5.1.x design files for the OpenPyroJet Controller Board. 

Controller Board:
-----------------

V0.7:
Production: JLCPCB, 2 Layer, 1.6mm, Black
Date:  2022-06-14
 
Done: added OLED 128x128px M2 mounting hole to PCB
Done: changed R4 from 10uF to 100nF so Rotary Encoder would work CCW

V0.6:
Production: JLCPCB, 2 Layer, 1.6mm, Blue
Date:  2022-05-11

* would it be handy to include a set of 4 DIP switches for easy user/program config? (not enough spare GPIO for this)
Done: move the M3 OLED screen mounting hole a bit downwards 0.5mm
Done: move RGB LED to otherside of board to make it easier to be seen.
Done: rotate D3+R8 (buzzer) to RH or LH side of buzzer
Done: swap the 4 x 0402 resistors to 0603, to make it easier for people to assemble
Done: change UART: EN & IO0 labels to match ESP32: RESET & BOOT
Done: remove i2C being sent to Driver board and replace with SPI-4 pin
Done: swap out 20pin connector for a 24 pin connector to the Driver board
Done: break out all non-used GPIO to a Test Point (TP).
Done: add connector for printhead pump circulation via PWM on GPIO26 to external board
Done: fix Green LED text (extra L) on back of PCB
Done: add a white box for S/N area to back of PCB
Done: add User Switch GPIO text to back of PCB:  GPIO26

V0.5:
Production: JLCPCB, 4 Layer, 1.6mm, Green
Date:  2022-03-22

Initial version.
Done: use a ESP32-Wroom-32E 16MB Flash MCU
Done: Rotary Encoder for menu selection
Done: 128x64px i2C OLED screen
Done: add a 20 pin (2 x 10 pin header) connector to mate with Driver board
Done: Micro USB connector for programming via CP2102 UART

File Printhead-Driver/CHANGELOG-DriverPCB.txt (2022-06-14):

This directory contains KiCAD 5.1.x design files for a set of PCB's that make up the OpenPyroJet Gen 3.1 printhead. 

Driver Board:
-------------

V0.7:
Production: JLCPCB, 2 Layer, 1.6mm, Black
Date:  2022-06-12

Done: add another resistor in series with R15 (6V feedback voltage divider, so R15 can be tweeked.  Best to be 1150 ohms.  I have 1100 and 47 ohms, or 1000 + 150 Ohms.
Done: added test point for 5V Vrefence
Done: add a small power switch.  It just needs to turn the input MOSFET on/off
Done: add a test point at VSW voltage devider, to make it easier to read
Done: Look to add one of my 5V voltage reference (SOT23-3) IC's. Can do 15mA with a 6+V input voltage
Done: Read ADC128 datasheet on input filter values.  Need to add a 100 ohm resistor in series. Only done for the VSW Port 0 line.
Done: change R9 (88K) to 100K, R8 (12K) to 10K.  See calculation in LCSC order spreadsheet: 45V=4.09V; 24V=2.18V
Done: change 12V Zener footprint from 0805 to SOD-123

V0.6:
Production: JLCPCB, 2 Layer, 1.6mm, Blue
Date:  2022-05-11

* how to bring out nozzle GPIO + Current Sense resistors to TP's so we can use Dupont connectors to monitor them?  Just continue mounting on the Sense resistor.
* when in program mode, the ESP32 drives one of the nozzles one?  Which one?
Done: Added a GPIO26 PWM pin output for pump control
Done: replace 24V input connector with a SMD XH connector
Done:  safely discharge VSW caps (VSW Volt Divider will do this)
Done: mark each driver IC with Nozzle number on silkscreen layer
Done: leave off the extra motor driver 100nF VSW rated caps. Looks to be working fine without
Done: add Nozzle # to bottom of nozzle connector
Done: add a white box for S/N area to back of PCB
Done:  Add filer caps foorptints to Motor Sense resisor and ADC inputs.
Done: change 0.03 ohm motor driver sense resistors from 2512 to 1206 0.04 ohm 
Done: ditch the MA1101 current sensor
Done: Add INA180 to R2 (0.04 ohms) and feed each into the ADC128
Done: should I have extra ADC power filtering?  1uH inductor vs. 120m Ohm FB?
Done: Do we want a fuse for 24V input? 
Done: change 0805 LEDs and resistors to 0603
Done: add VCC - 3.3V to U9 pin 10!
Done: change 22uF/50V cap C37 to 1206 size 22uF/50V and order them
Done: change 1/2 the 100nF Caps for Motor driver IC's to 100V
Done: change both 50V 100nF caps to 100V
Done: remove one large 1000uF  cap
Done: look at changing to a SPI based ADC128 IC. Allows seperate 5V/3.3V inputs.
Done: change 3.3V DC-DC converter to 6V + filter o/p.  Then use a 5V LDO + 3.3V LDO to help minimise noise and line ripple
Done: add a voltage divider to measure (via SPI ADC) the VSW voltage from the PSU?
Done: could put a RU30L30 mosfet as a power reversal protection on the input. Remove D2

V0.5:
Production: JLCPCB, 4 Layer, 1.6mm, Green
Date:  2022-03-22

Initial version.
Done: add a MA1101 current sensor to monitor VSW current.
Done: Add a ADC121 ADC to measure MA1101 output
Done: use TMI8870 45V @ 3.6A Motor Driver IC's to drive each of the Nozzle filaments
Done: add a XL6019 24V to 45V @ 4A DC-DC boost converter
Done: add a MC34063 24V to 6V DC-DC buck converter
Done: add 5V and 3.3V LDO's.

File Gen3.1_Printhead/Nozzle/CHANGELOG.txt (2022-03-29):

This directory contains KiCAD 5.1.x design files for a set of PCB's that make up the OpenPyroJet Gen 3.1 printhead. 
 
The directory could be better named as Printhead (as opposed to Nozzle), but I believe thats hard to do once a KiCAD project has been started?

Printhead PCB Versions:
-------------

Gen3.1b:
Production: JLCPCB, 2 Layer, 1.6mm, Green
Date:  2022-0330

* change the Nozzle PCB screw holes from M1.27 to 0.635mm
* label each PCB with a letter, ie: A, B, C & D.  This will make referencing them easier.

Gen3.1a:
Production: JLCPCB, 2 Layer, 1.6mm, Green
Date:  2022-03-29

* swapped the Connector PCB 1.27mm inlet holes for 6 x 1mm and 2 x 0.8mm holes.  This gives thicker filament pads (0.4mm wide).

Gen3.1:
Production: JLCPCB, 2 Layer, 1.6mm, Green
Date:  2022-03-27

* initial version, with one of PCB PCB produced

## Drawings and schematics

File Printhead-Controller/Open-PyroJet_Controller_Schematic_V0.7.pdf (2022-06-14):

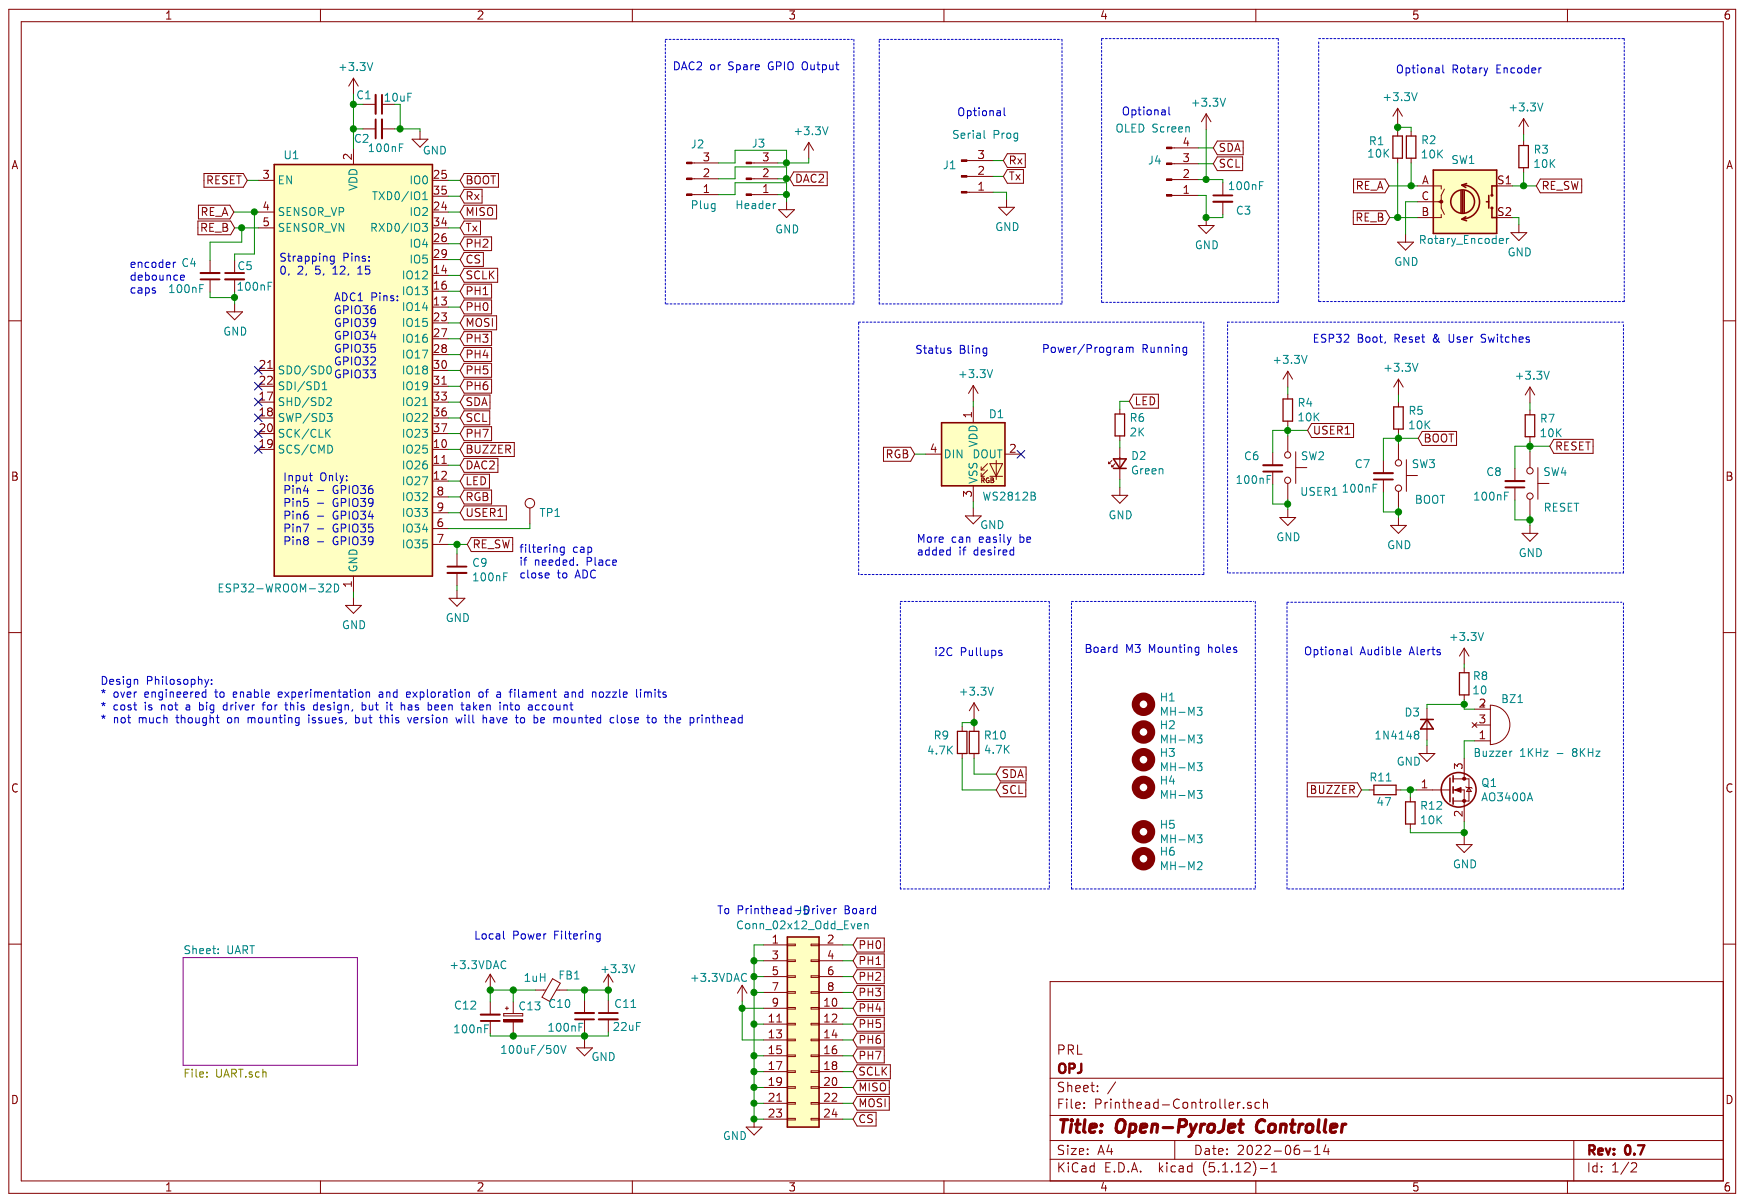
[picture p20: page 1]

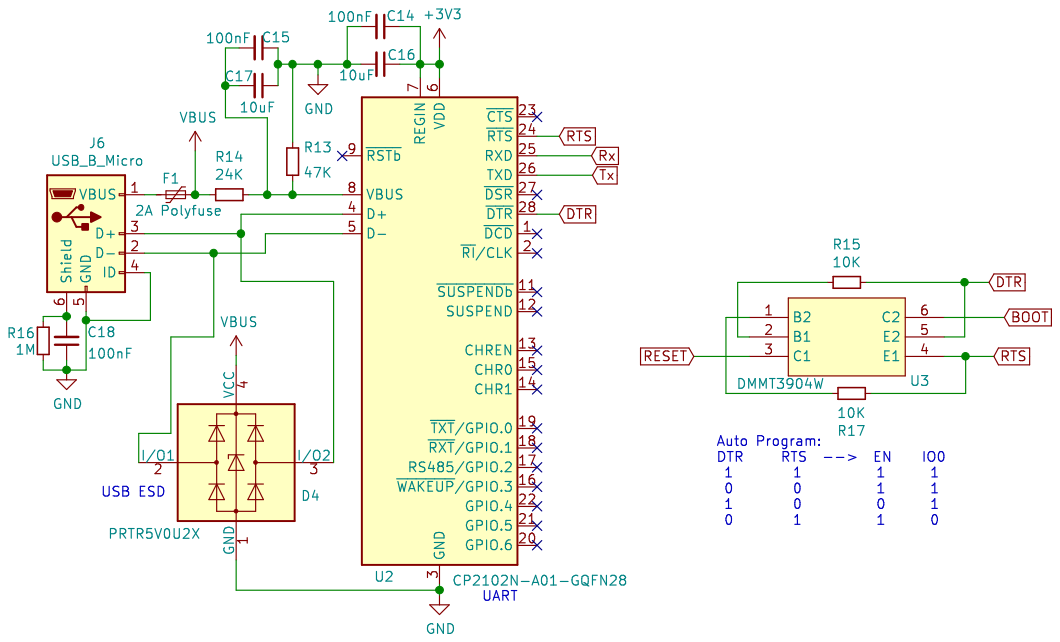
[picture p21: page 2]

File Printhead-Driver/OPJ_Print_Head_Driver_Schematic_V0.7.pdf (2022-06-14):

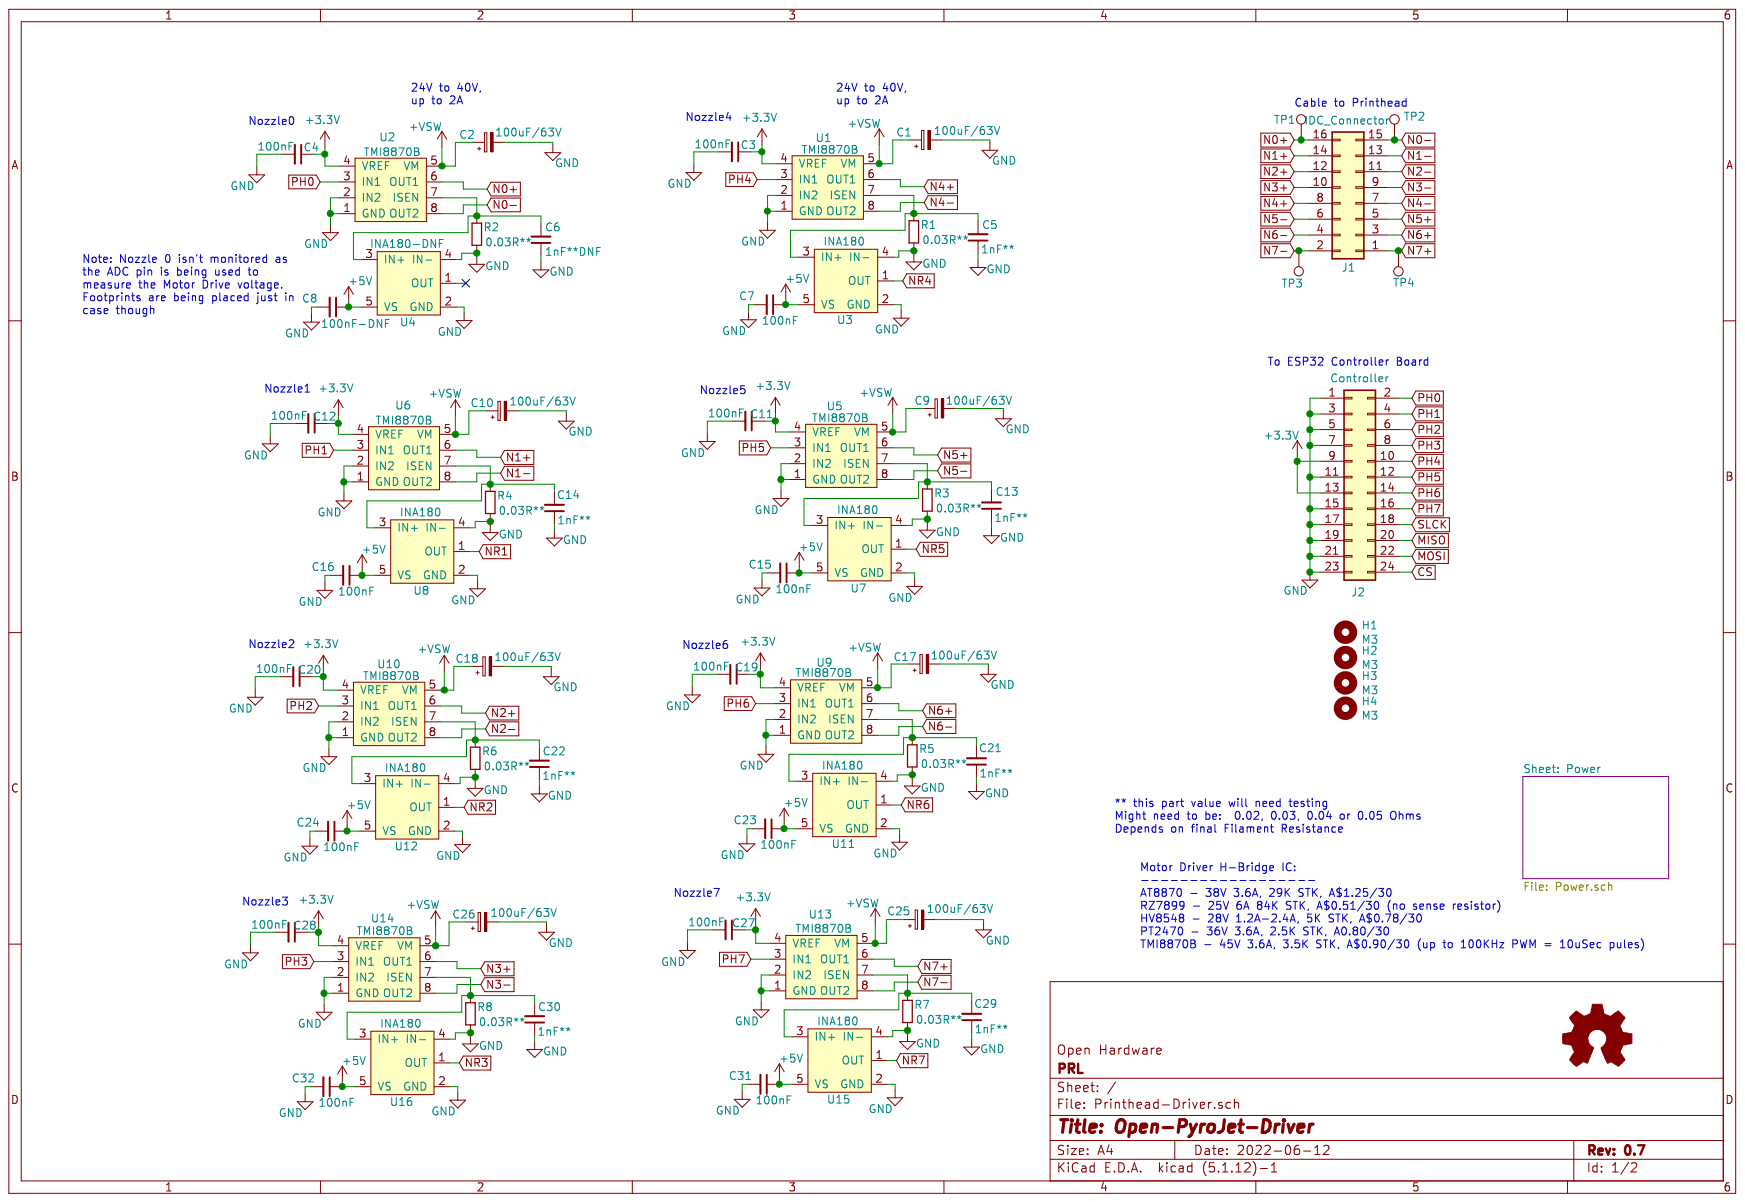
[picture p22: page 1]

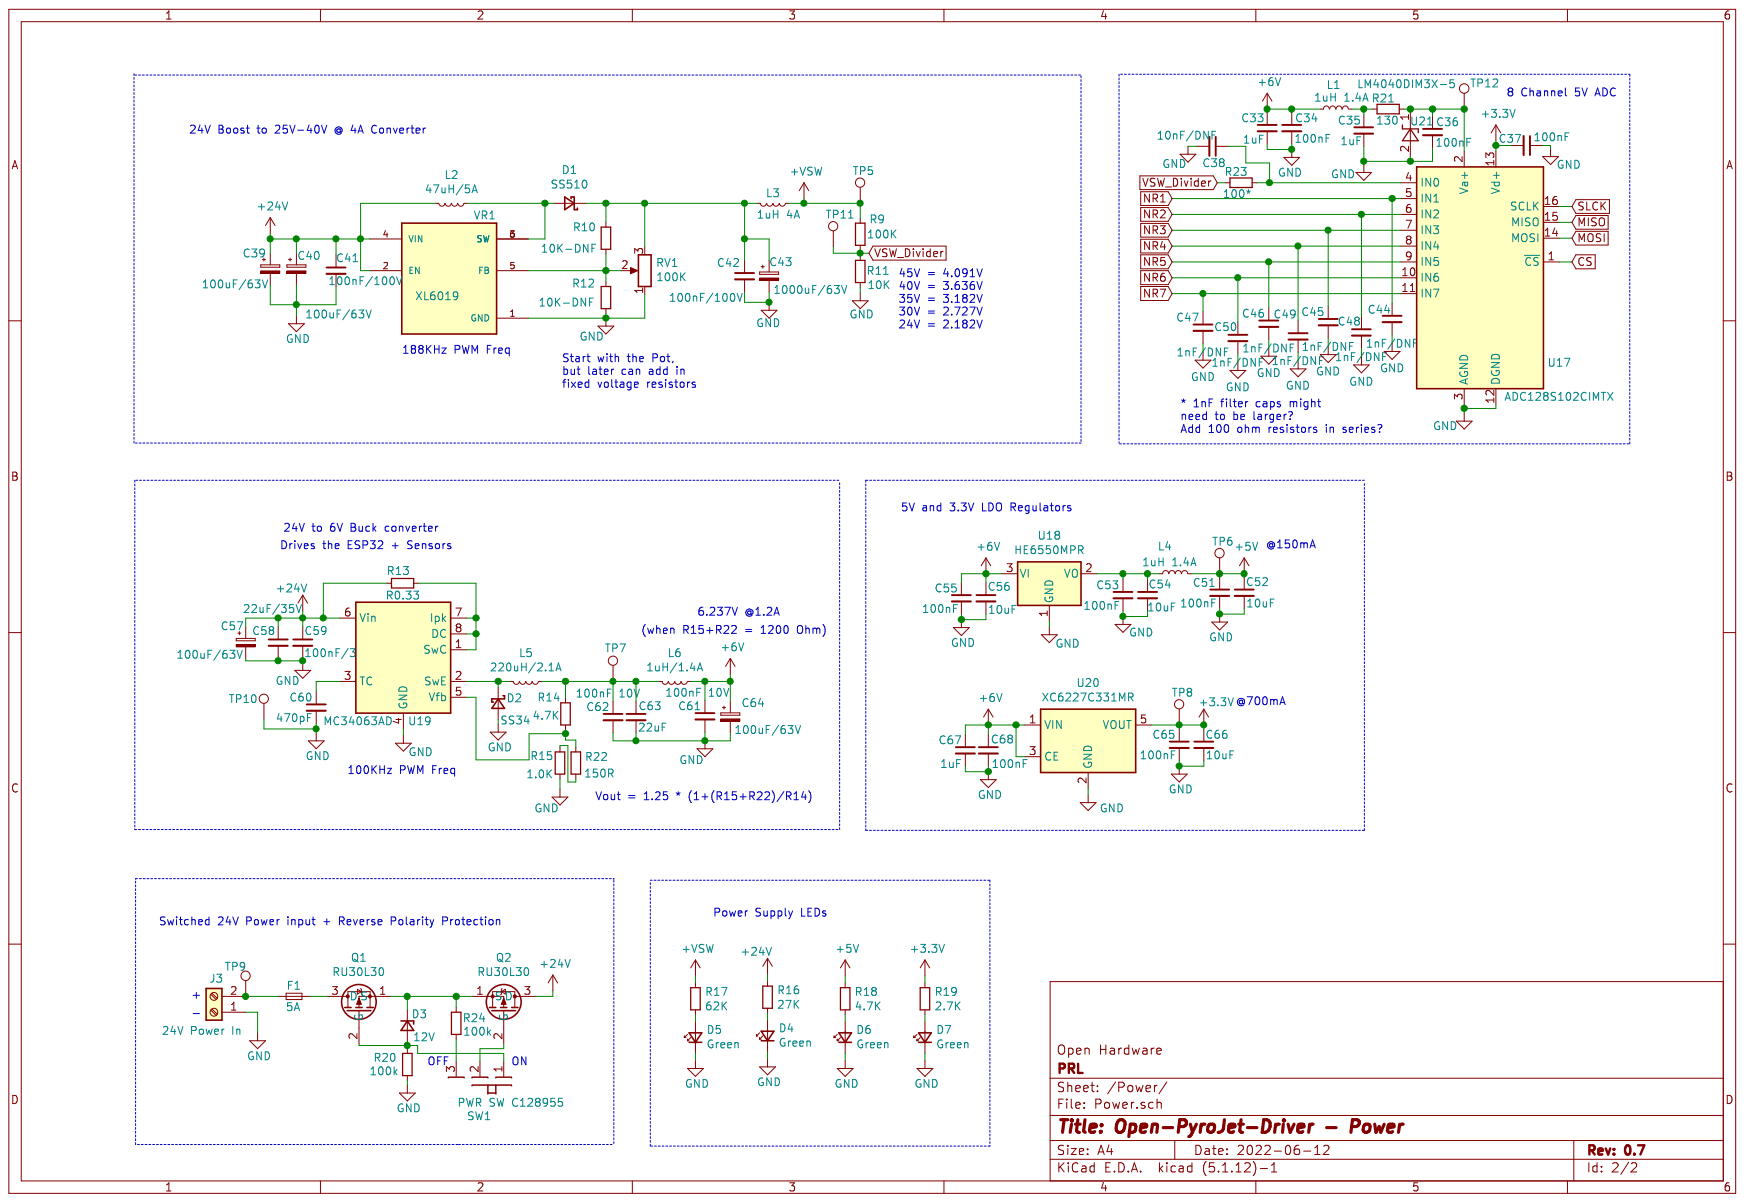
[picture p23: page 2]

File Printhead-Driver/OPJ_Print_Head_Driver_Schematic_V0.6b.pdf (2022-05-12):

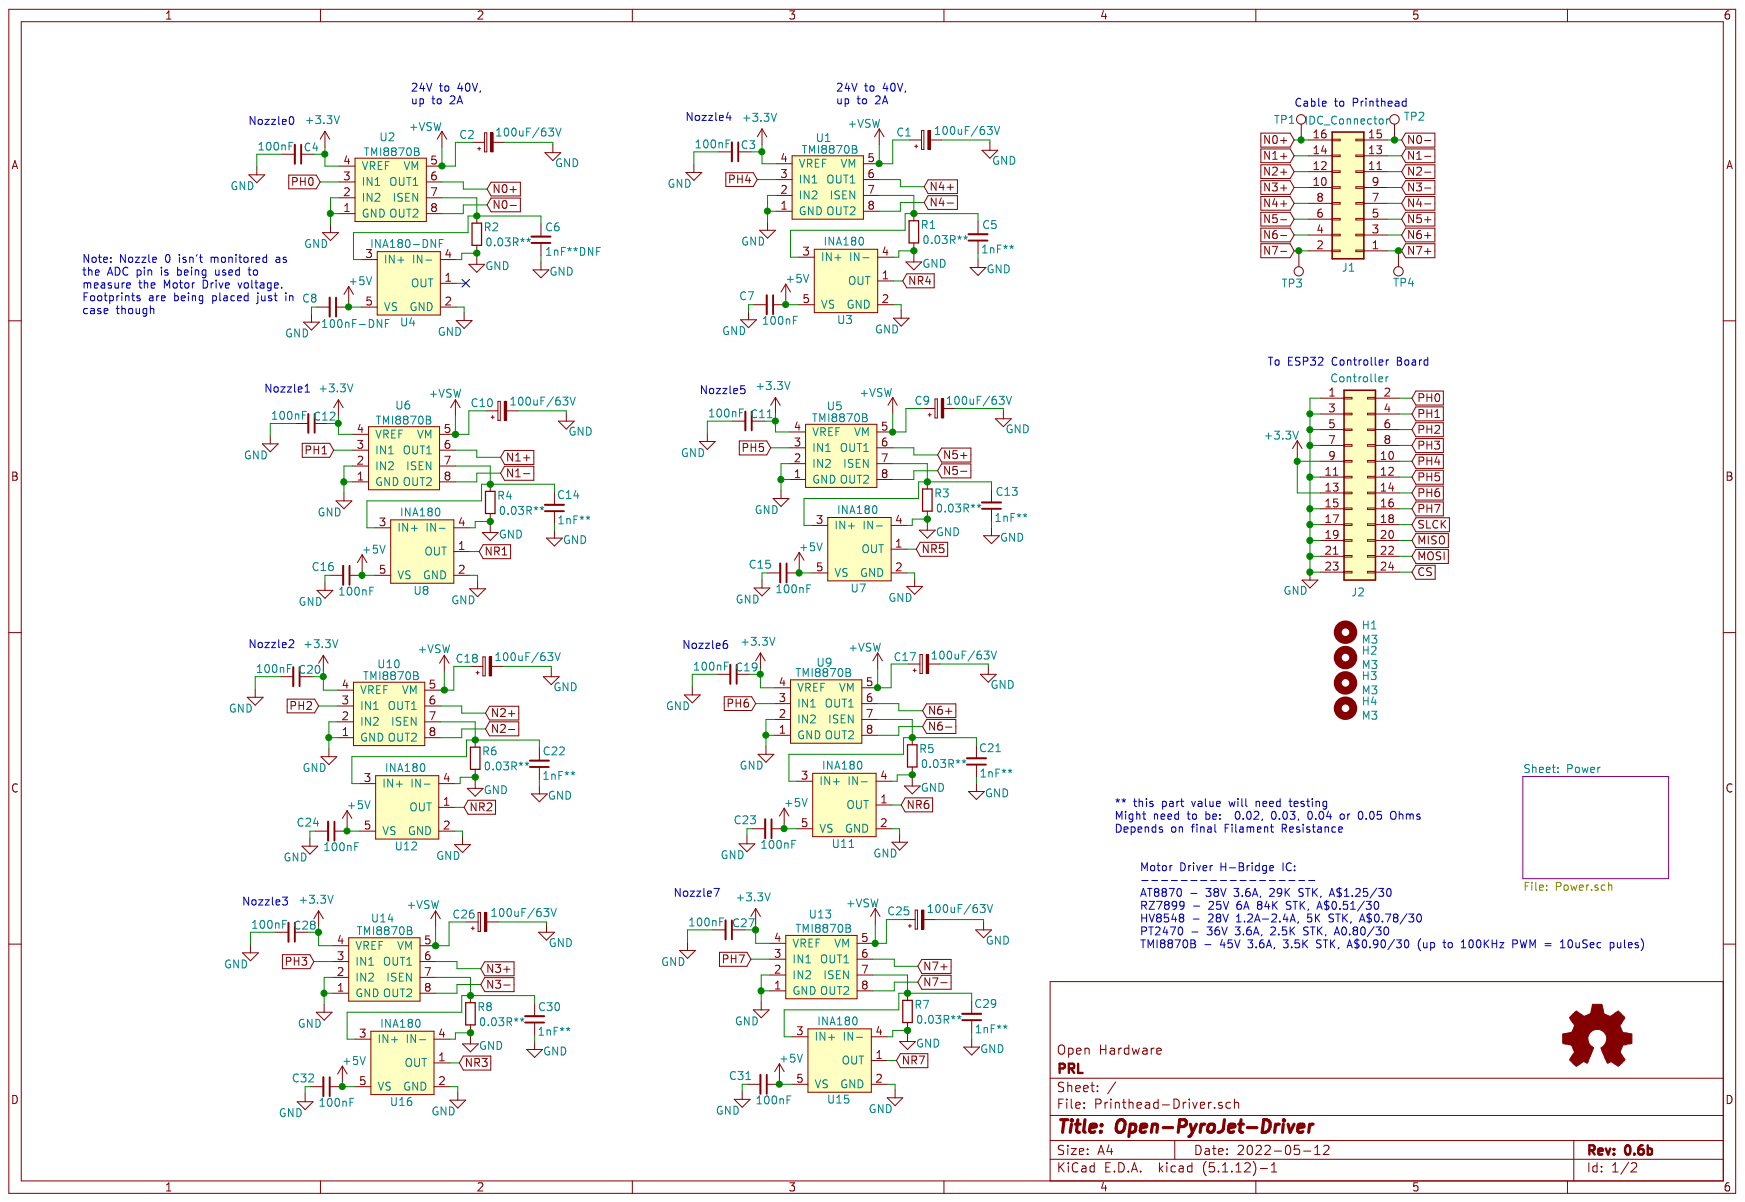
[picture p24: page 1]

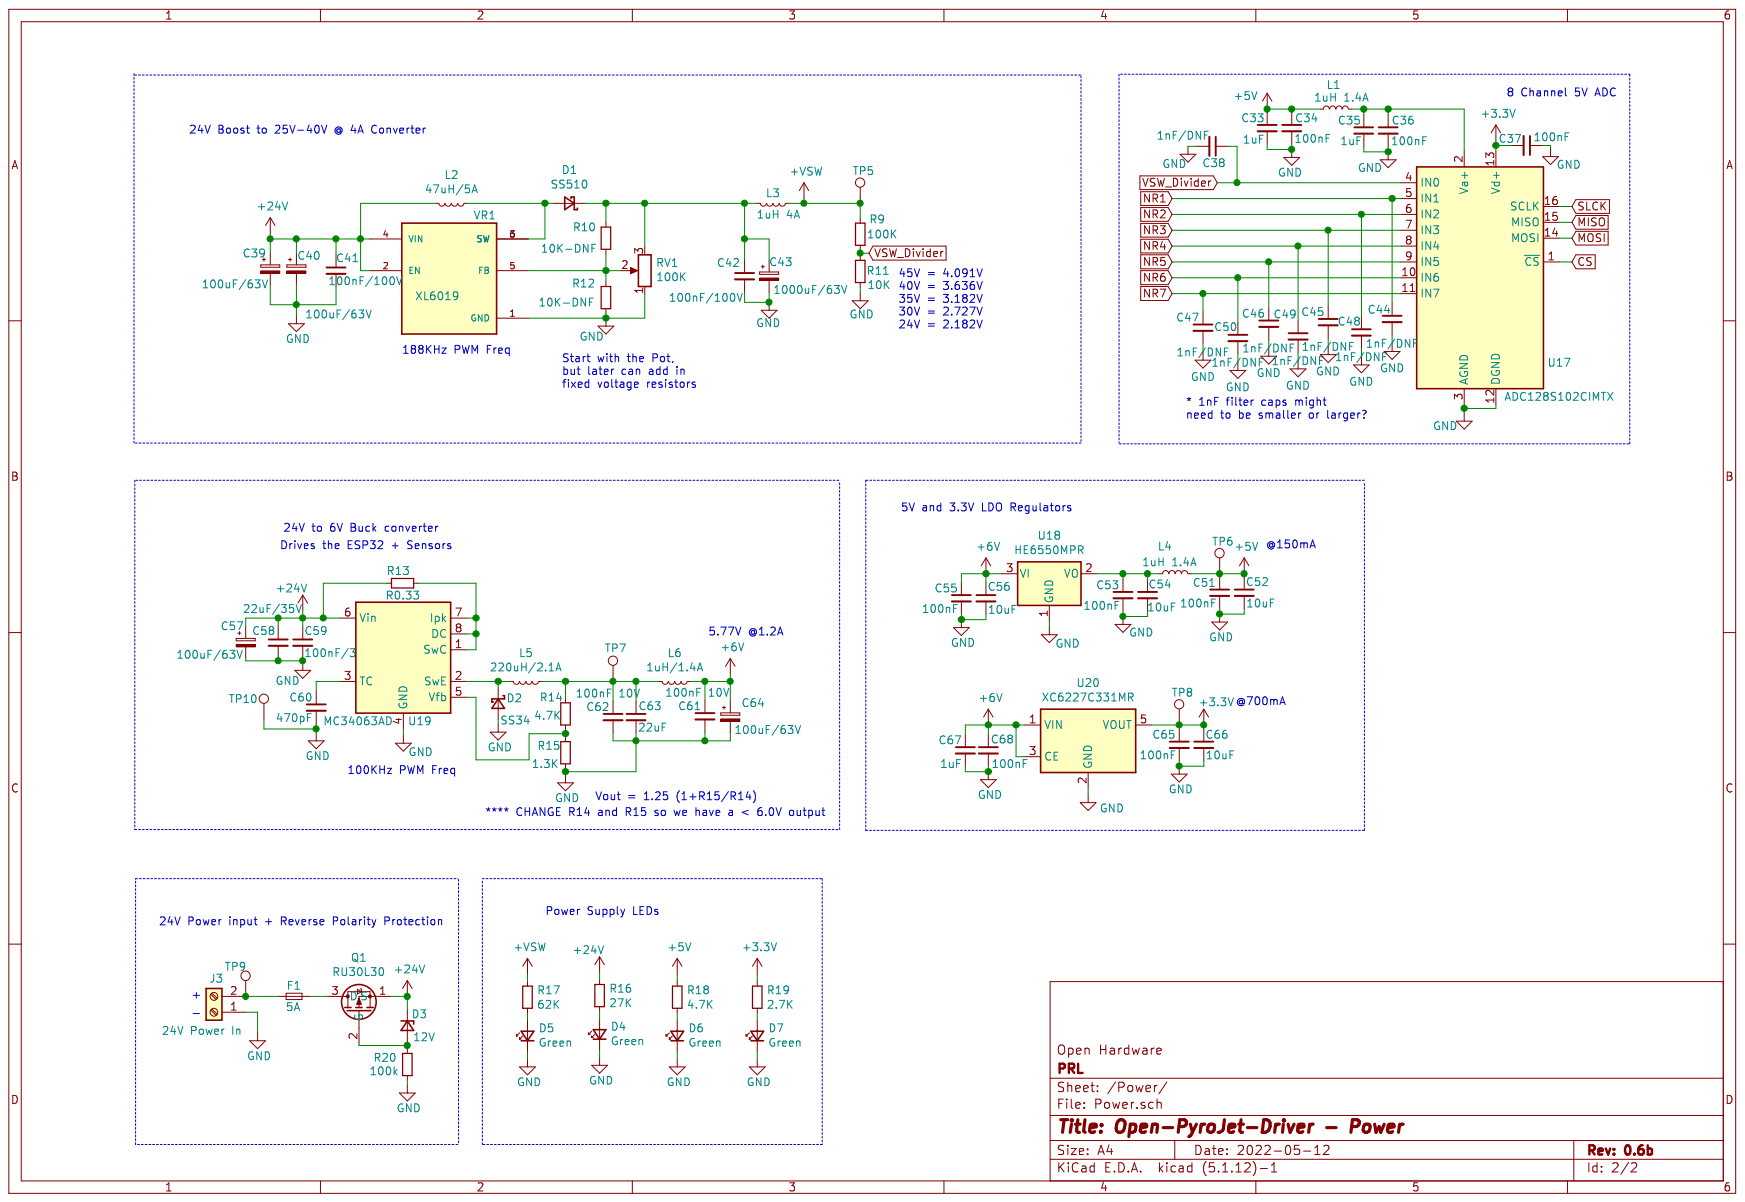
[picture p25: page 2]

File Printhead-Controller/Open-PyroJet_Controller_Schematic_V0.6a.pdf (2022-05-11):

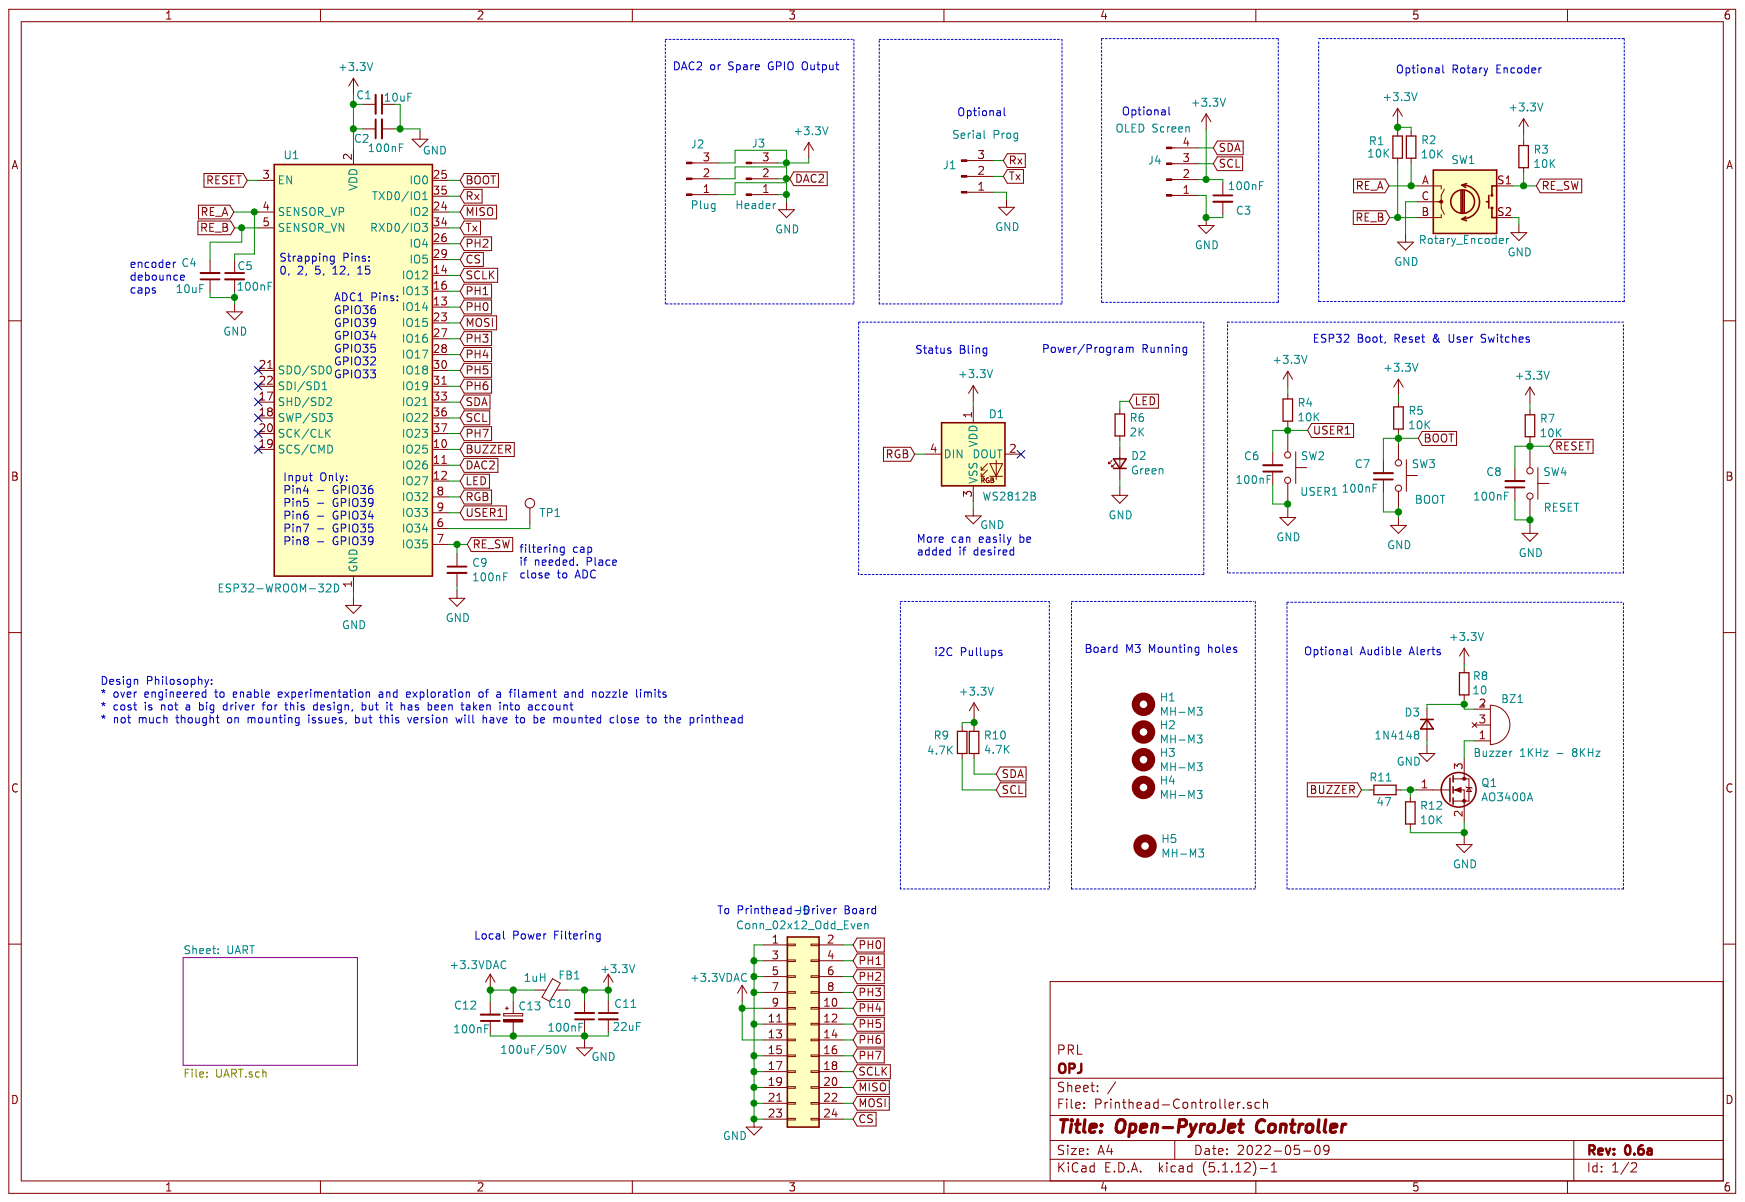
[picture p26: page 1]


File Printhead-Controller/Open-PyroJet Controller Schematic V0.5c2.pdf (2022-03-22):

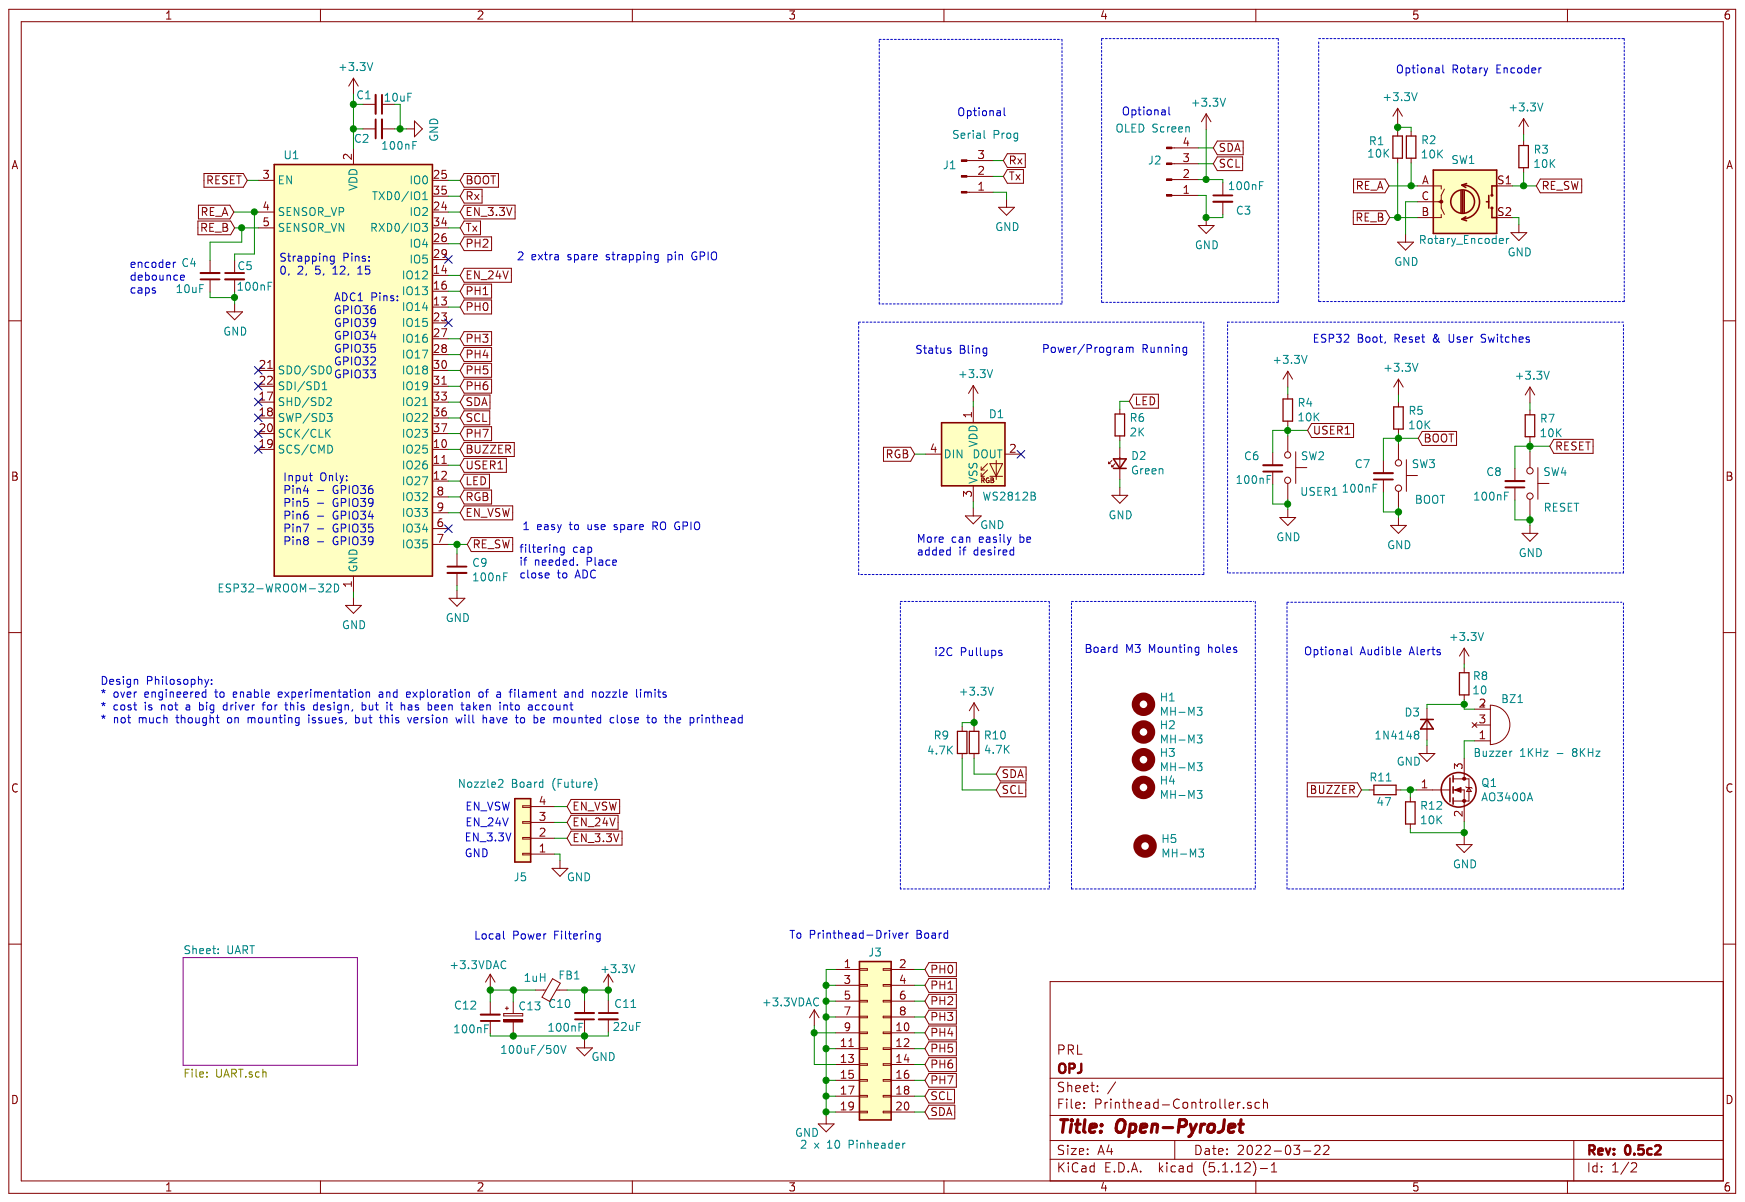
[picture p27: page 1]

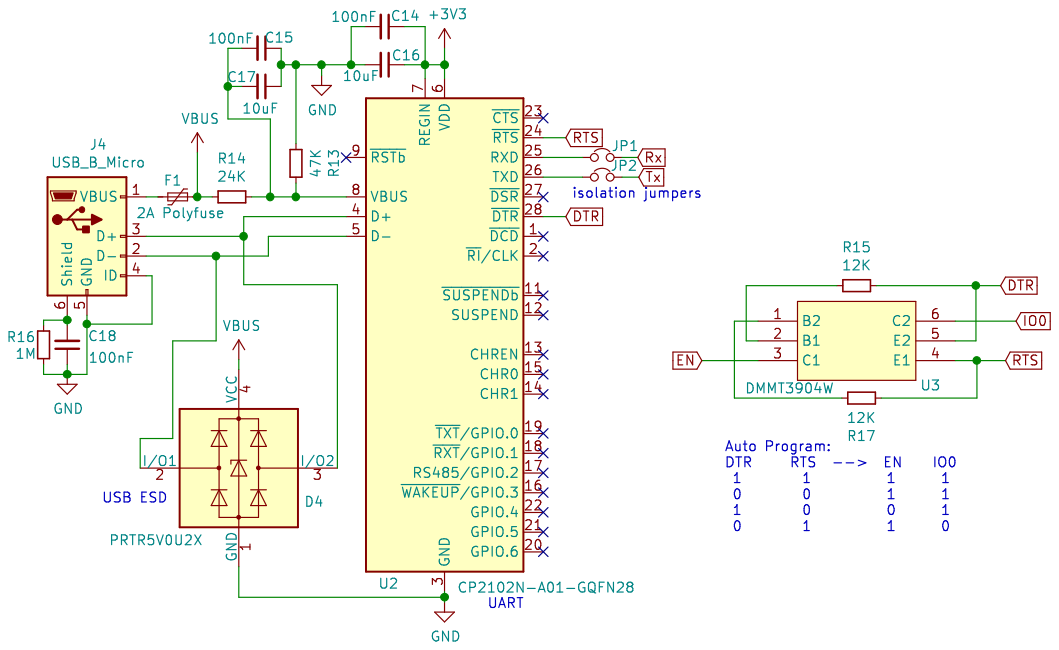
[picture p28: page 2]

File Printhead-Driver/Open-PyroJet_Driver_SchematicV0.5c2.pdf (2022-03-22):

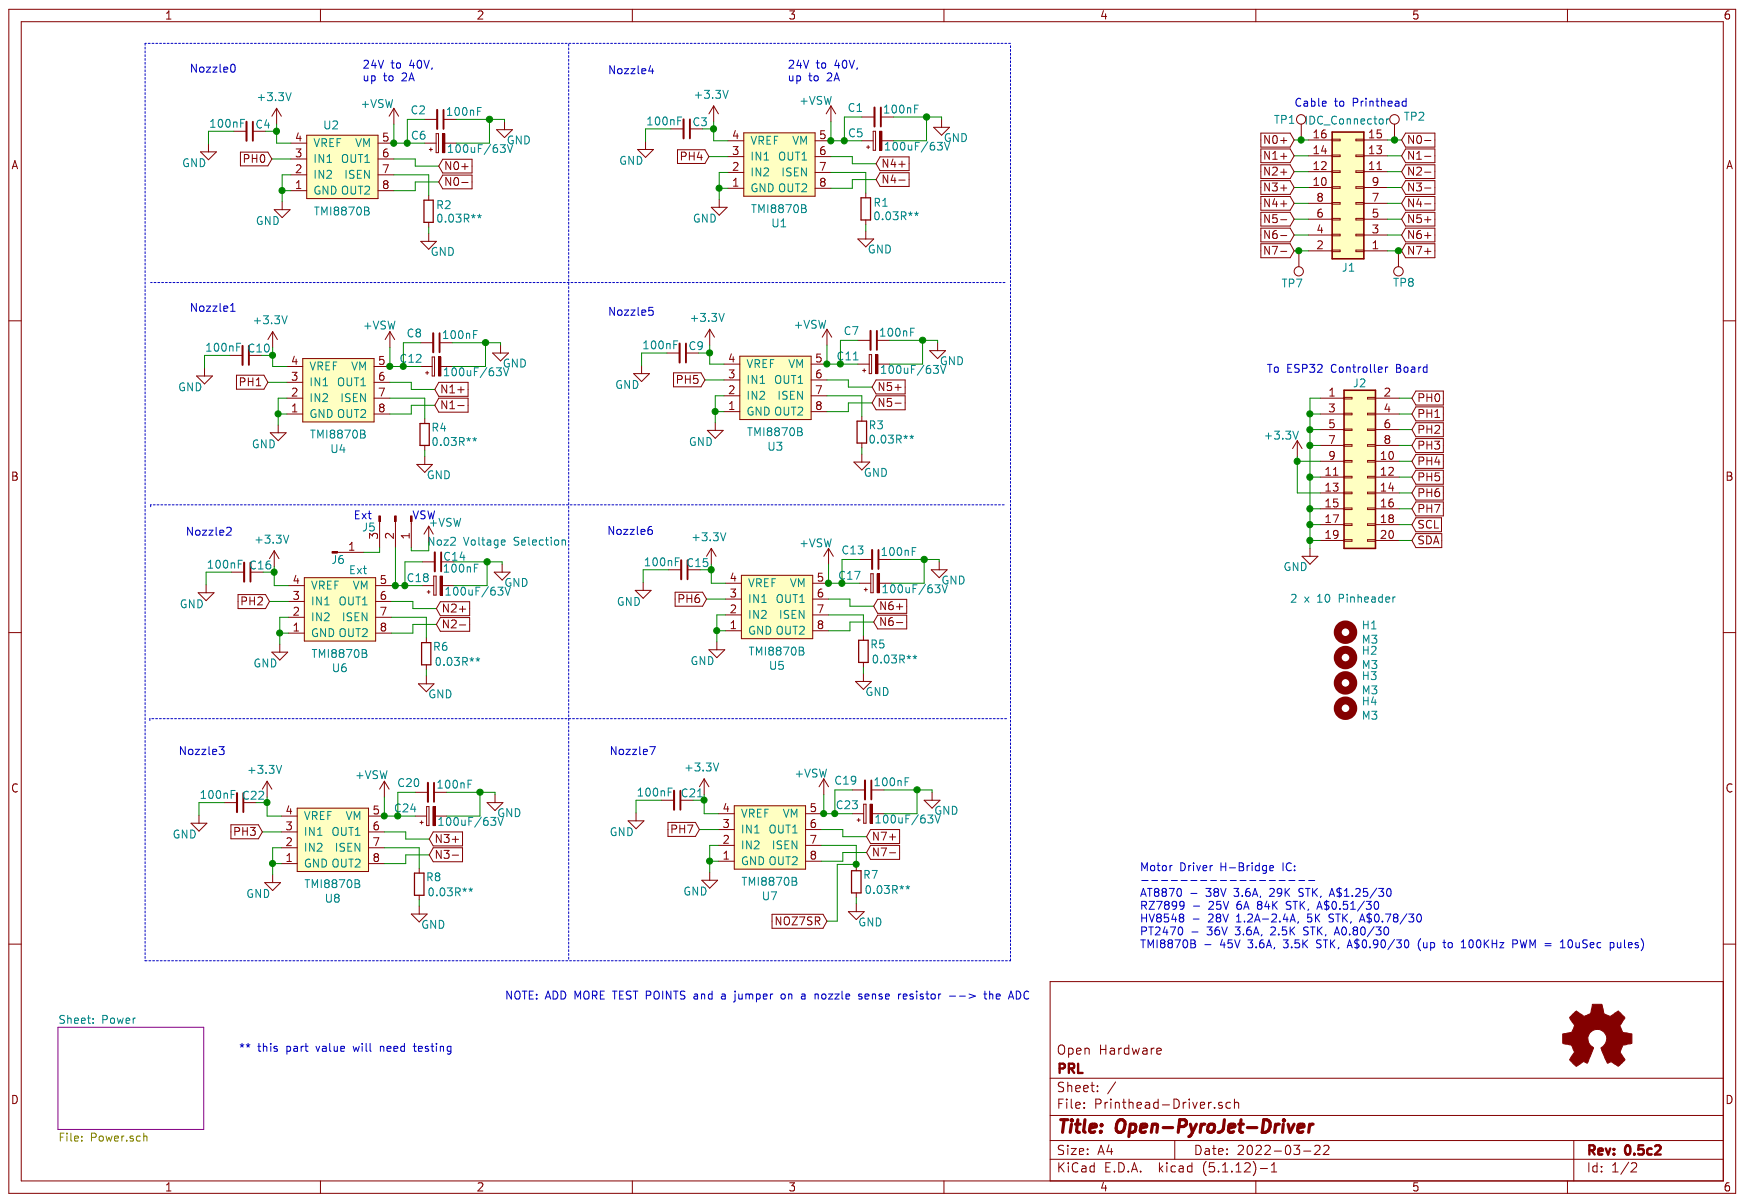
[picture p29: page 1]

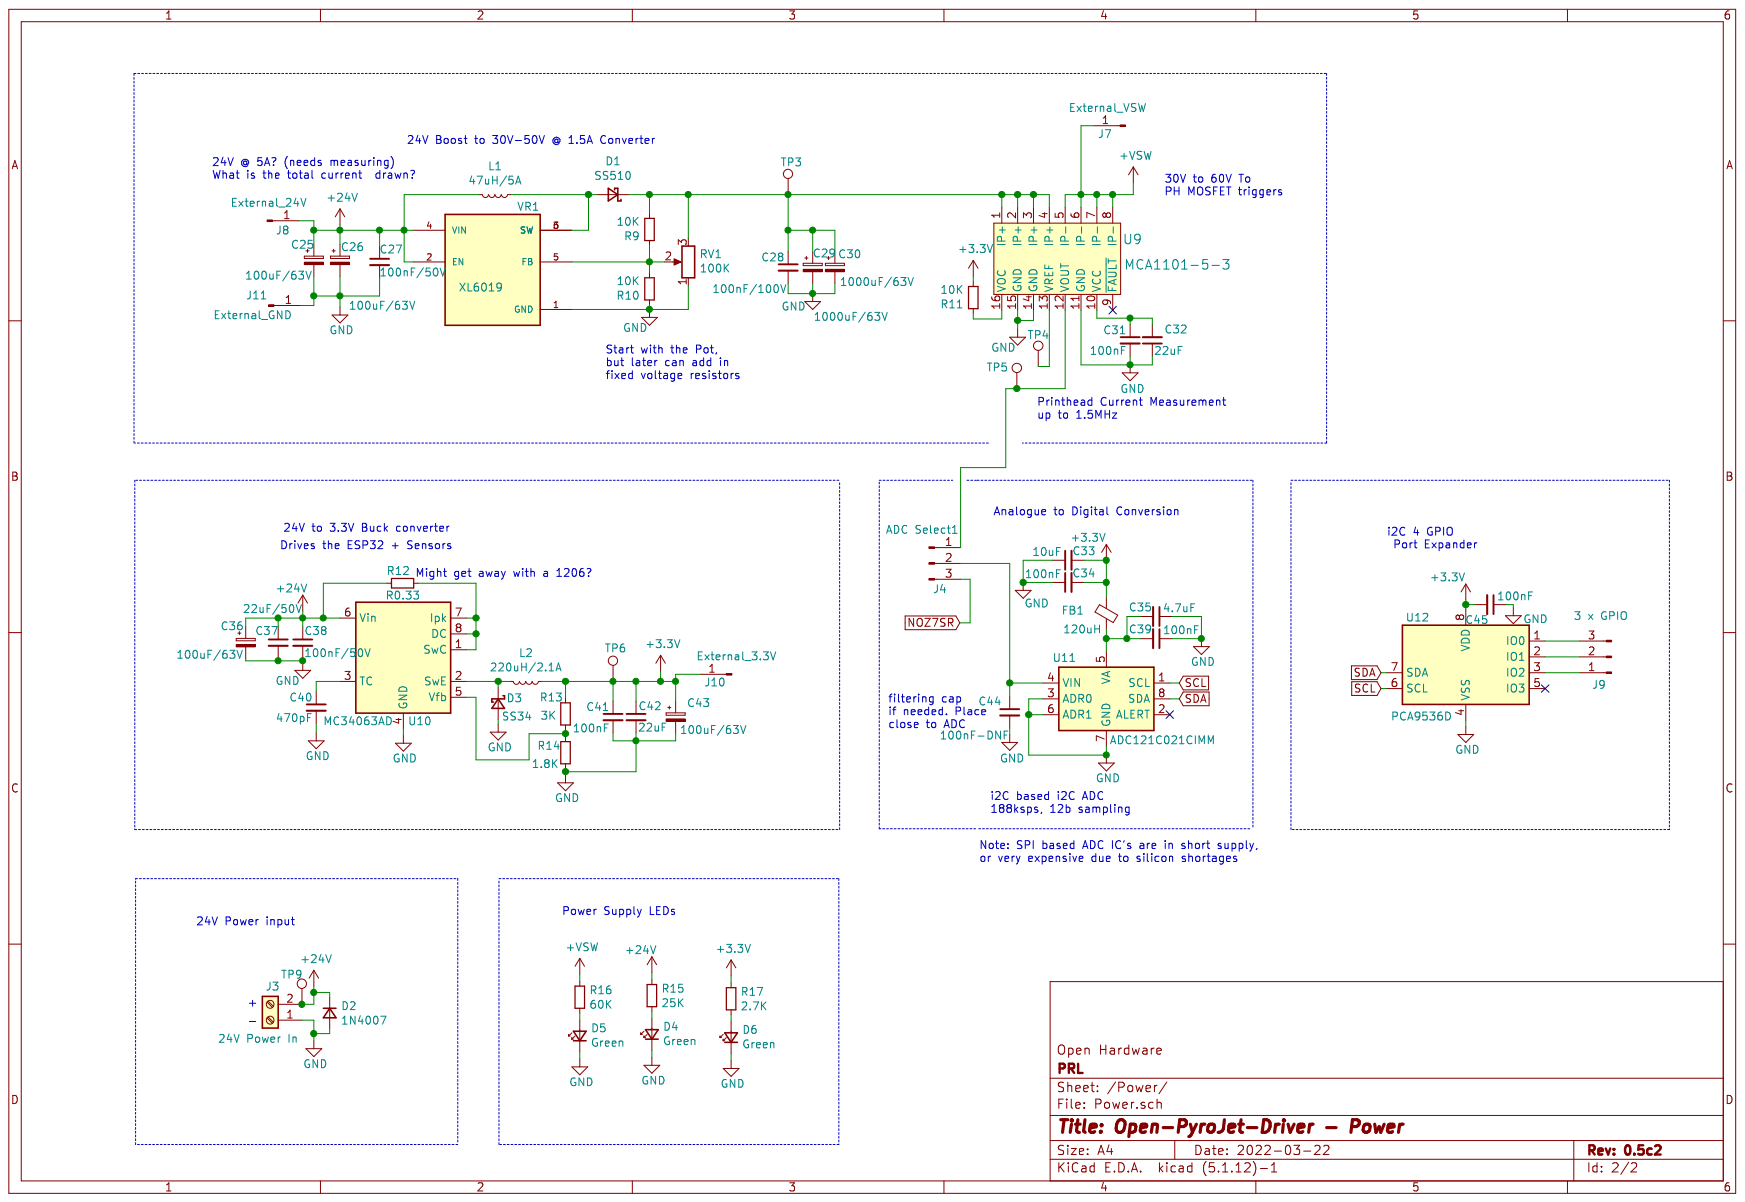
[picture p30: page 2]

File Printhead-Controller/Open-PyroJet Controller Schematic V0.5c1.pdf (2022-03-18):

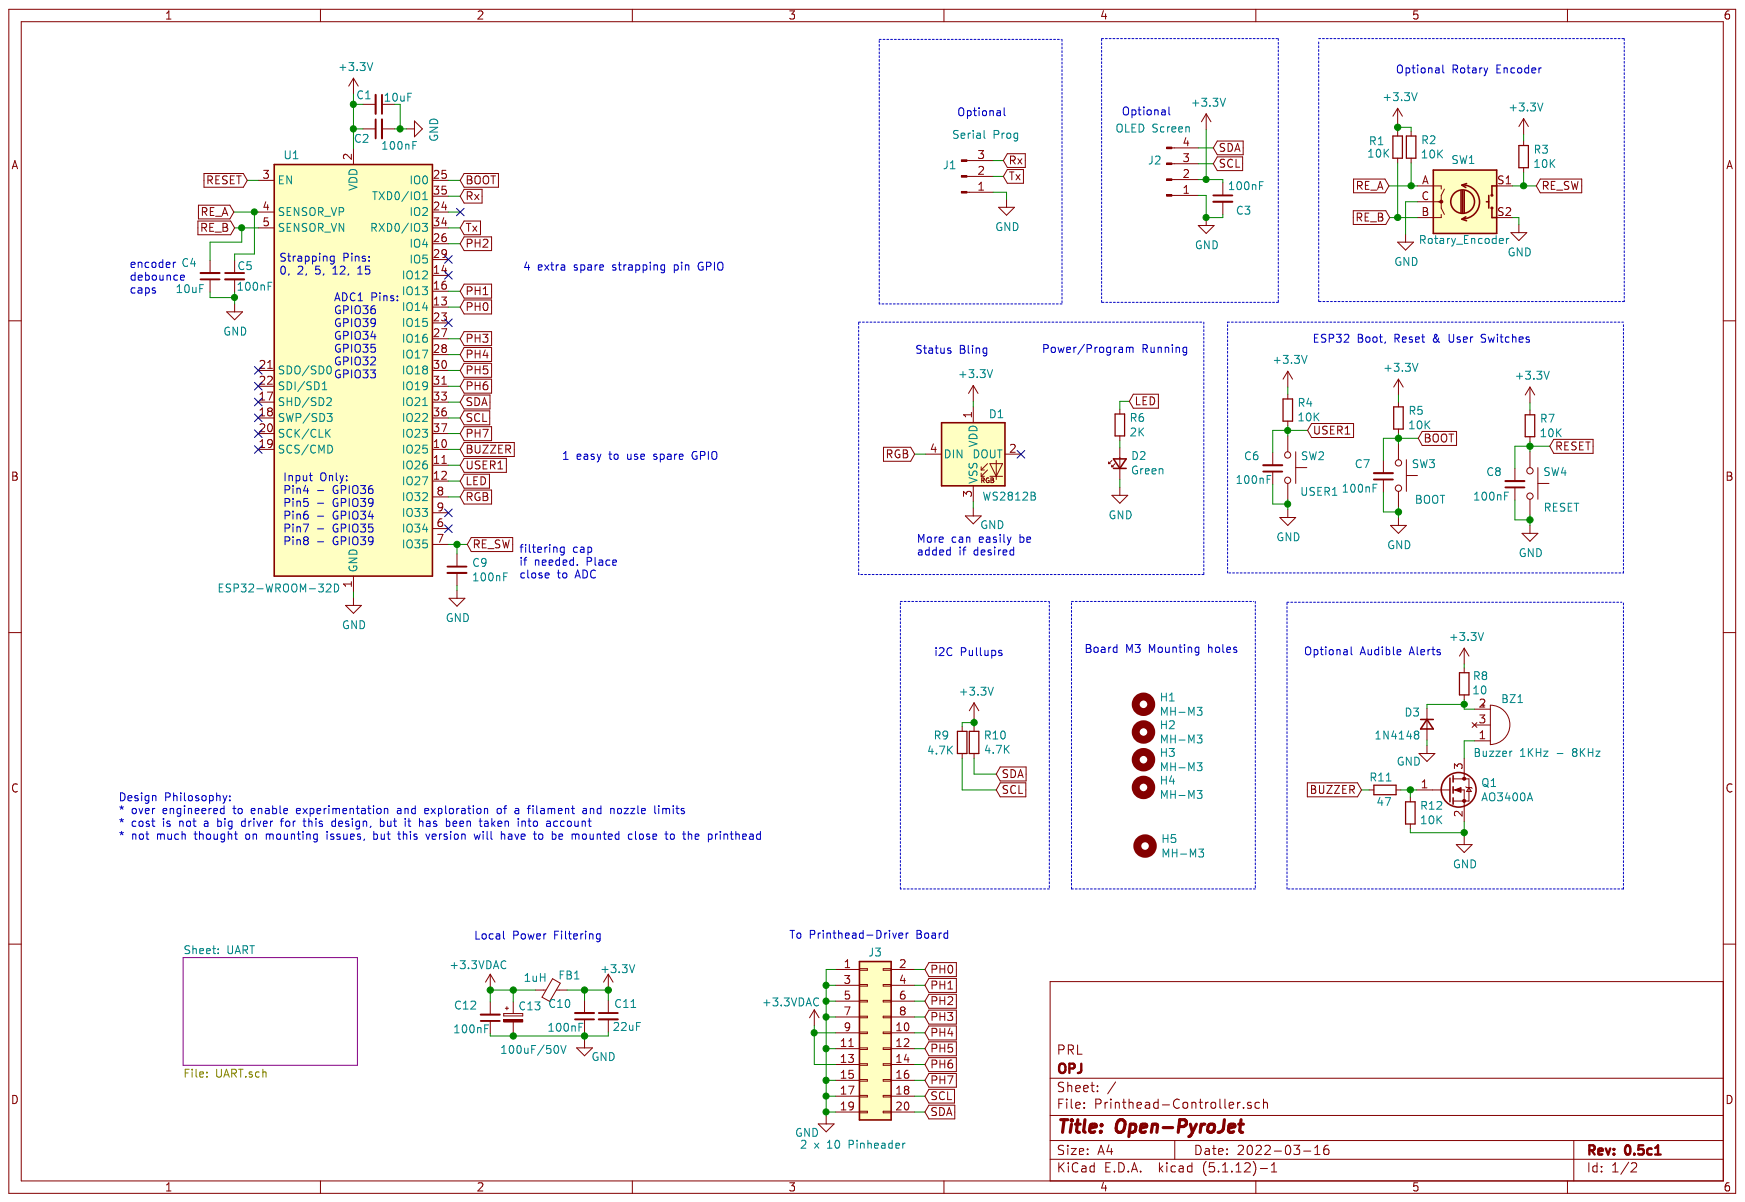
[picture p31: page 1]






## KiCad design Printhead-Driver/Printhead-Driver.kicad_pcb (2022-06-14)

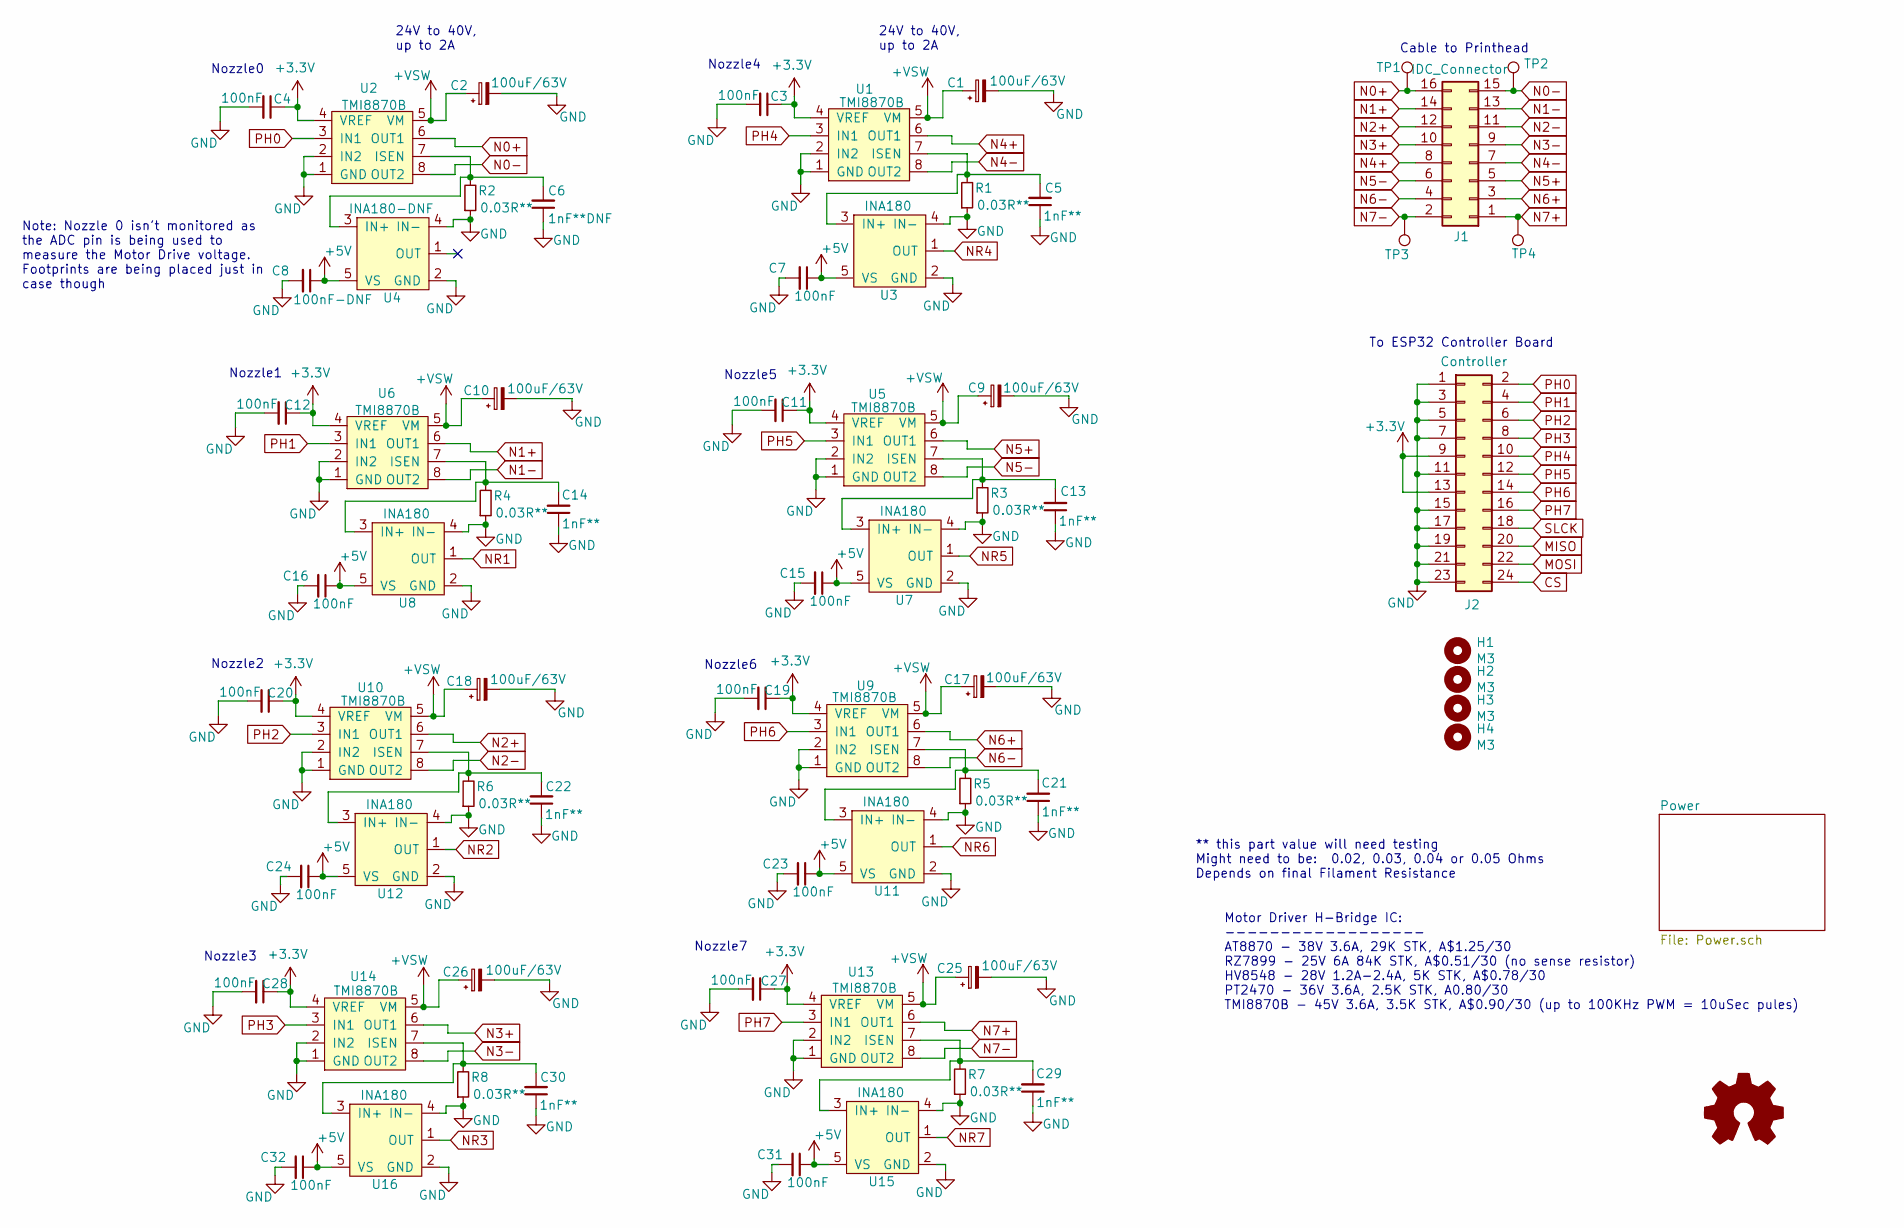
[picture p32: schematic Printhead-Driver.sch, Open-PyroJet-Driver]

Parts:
C1, C2, C9, C10, C17, C18, C25, C26: 100uF/63V; CP_Radial_D8.0mm_P3.50mm
C3, C4, C7, C11, C12, C15, C16, C19, C20, C23, C24, C27, C28, C31, C32: 100nF; C_0603_1608Metric
C5, C13, C14, C21, C22, C29, C30: 1nF**; C_0603_1608Metric
C6: 1nF**DNF; C_0603_1608Metric
C8: 100nF-DNF; C_0603_1608Metric
H1, H2, H3, H4: M3; MountingHole_3.2mm_M3
J1: IDC_Connector; IDC-Header_2x08_P2.54mm_Horizontal
J2: Controller; PinHeader_2x12_P2.54mm_Vertical
R1, R2, R3, R4, R5, R6, R7, R8: 0.03R**; R_1206_3216Metric
TP1, TP2, TP3, TP4: TestPoint; TestPoint_THTPad_1.5x1.5mm_Drill0.7mm
U1, U2, U5, U6, U9, U10, U13, U14: TMI8870B; HSOP-8-1EP_3.9x4.9mm_P1.27mm_EP2.41x3.1mm_ThermalVias
U3, U7, U8, U11, U12, U15, U16: INA180; SOT-23-5
U4: INA180-DNF; SOT-23-5

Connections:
+3V3: C3.1, C4.1, C11.1, C12.1, C19.1, C20.1, C27.1, C28.1, J2.9, J2.13, U1.4 (VREF), U2.4 (VREF), U5.4 (VREF), U6.4 (VREF), U9.4 (VREF), U10.4 (VREF), U13.4 (VREF), U14.4 (VREF); also elsewhere on the board
+5V: C7.1, C8.1, C15.1, C16.1, C23.1, C24.1, C31.1, C32.1, U3.5 (VS), U4.5 (VS), U7.5 (VS), U8.5 (VS), U11.5 (VS), U12.5 (VS), U15.5 (VS), U16.5 (VS); also elsewhere on the board
+VSW: C1.1, C2.1, C9.1, C10.1, C17.1, C18.1, C25.1, C26.1, U1.5 (VM), U2.5 (VM), U5.5 (VM), U6.5 (VM), U9.5 (VM), U10.5 (VM), U13.5 (VM), U14.5 (VM); also elsewhere on the board
CS: J2.24; also elsewhere on the board
GND: C1.2, C2.2, C3.2, C4.2, C5.1, C6.1, C7.2, C8.2, C9.2, C10.2, C11.2, C12.2, C13.1, C14.1, C15.2, C16.2, C17.2, C18.2, C19.2, C20.2, C21.1, C22.1, C23.2, C24.2, C25.2, C26.2, C27.2, C28.2, C29.1, C30.1, C31.2, C32.2, J2.1, J2.3, J2.5, J2.7, J2.11, J2.15, J2.17, J2.19, J2.21, J2.23, R1.1, R2.1, R3.1, R4.1, R5.1, R6.1, R7.1, R8.1, U1.1 (GND), U1.2 (IN2), U2.1 (GND), U2.2 (IN2), U3.2 (GND), U3.4 (IN-), U4.2 (GND), U4.4 (IN-), U5.1 (GND), U5.2 (IN2), U6.1 (GND), U6.2 (IN2), U7.2 (GND), U7.4 (IN-), U8.2 (GND), U8.4 (IN-), U9.1 (GND), U9.2 (IN2), U10.1 (GND), U10.2 (IN2), U11.2 (GND), U11.4 (IN-), U12.2 (GND), U12.4 (IN-), U13.1 (GND), U13.2 (IN2), U14.1 (GND), U14.2 (IN2), U15.2 (GND), U15.4 (IN-), U16.2 (GND), U16.4 (IN-); also elsewhere on the board
MISO: J2.20; also elsewhere on the board
MOSI: J2.22; also elsewhere on the board
N0+: J1.16, TP1.1, U2.6 (OUT1)
N0-: J1.15, TP2.1, U2.8 (OUT2)
N1+: J1.14, U6.6 (OUT1)
N1-: J1.13, U6.8 (OUT2)
N2+: J1.12, U10.6 (OUT1)
N2-: J1.11, U10.8 (OUT2)
N3+: J1.10, U14.6 (OUT1)
N3-: J1.9, U14.8 (OUT2)
N4+: J1.8, U1.6 (OUT1)
N4-: J1.7, U1.8 (OUT2)
N5+: J1.5, U5.6 (OUT1)
N5-: J1.6, U5.8 (OUT2)
N6+: J1.3, U9.6 (OUT1)
N6-: J1.4, U9.8 (OUT2)
N7+: J1.1, TP4.1, U13.6 (OUT1)
N7-: J1.2, TP3.1, U13.8 (OUT2)
NR1: U8.1 (OUT); also elsewhere on the board
NR2: U12.1 (OUT); also elsewhere on the board
NR3: U16.1 (OUT); also elsewhere on the board
NR4: U3.1 (OUT); also elsewhere on the board
NR5: U7.1 (OUT); also elsewhere on the board
NR6: U11.1 (OUT); also elsewhere on the board
NR7: U15.1 (OUT); also elsewhere on the board
unnamed: C5.2, R1.2, U1.7 (ISEN), U3.3 (IN+)
unnamed: C6.2, R2.2, U2.7 (ISEN), U4.3 (IN+)
unnamed: C13.2, R3.2, U5.7 (ISEN), U7.3 (IN+)
unnamed: C14.2, R4.2, U6.7 (ISEN), U8.3 (IN+)
unnamed: C21.2, R5.2, U9.7 (ISEN), U11.3 (IN+)
unnamed: C22.2, R6.2, U10.7 (ISEN), U12.3 (IN+)
unnamed: C29.2, R7.2, U13.7 (ISEN), U15.3 (IN+)
unnamed: C30.2, R8.2, U14.7 (ISEN), U16.3 (IN+)
PH0: J2.2, U2.3 (IN1)
PH1: J2.4, U6.3 (IN1)
PH2: J2.6, U10.3 (IN1)
PH3: J2.8, U14.3 (IN1)
PH4: J2.10, U1.3 (IN1)
PH5: J2.12, U5.3 (IN1)
PH6: J2.14, U9.3 (IN1)
PH7: J2.16, U13.3 (IN1)
SLCK: J2.18; also elsewhere on the board

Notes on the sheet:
24V to 40V, up to 2A
Motor Driver H-Bridge IC: ------------------ AT8870 - 38V 3.6A, 29K STK, A$1.25/30 RZ7899 - 25V 6A 84K STK, A$0.51/30 (no sense resistor) HV8548 - 28V 1.2A-2.4A, 5K STK, A$0.78/30 PT2470 - 36V 3.6A, 2.5K STK, A0.80/30 TMI8870B - 45V 3.6A, 3.5K STK, A$0.90/30 (up to 100KHz PWM = 10uSec pules)
** this part value will need testing Might need to be: 0.02, 0.03, 0.04 or 0.05 Ohms Depends on final Filament Resistance
Cable to Printhead
Nozzle0
Nozzle1
Nozzle2
Nozzle3
Nozzle7
Nozzle6
Nozzle5
Nozzle4
To ESP32 Controller Board
Note: Nozzle 0 isn't monitored as the ADC pin is being used to measure the Motor Drive voltage. Footprints are being placed just in case though

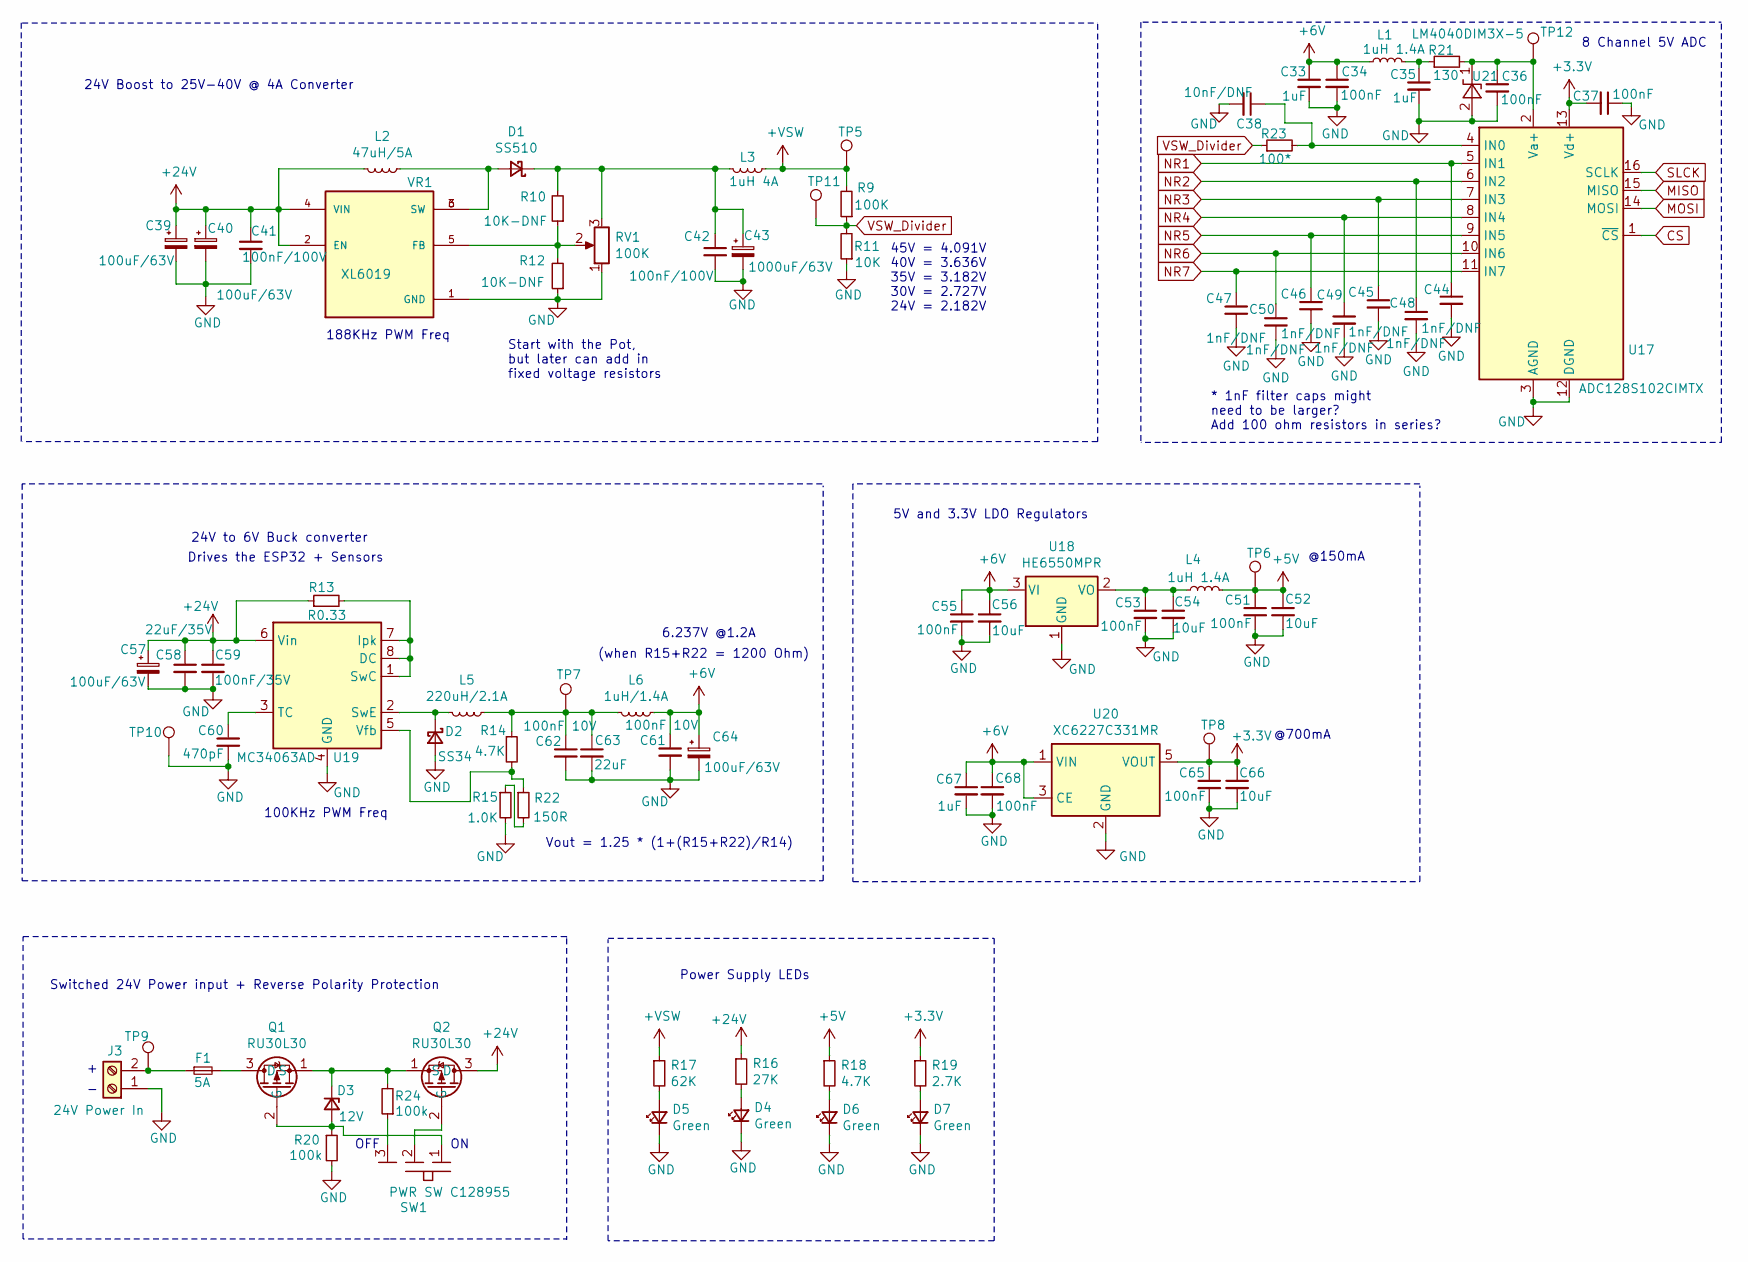
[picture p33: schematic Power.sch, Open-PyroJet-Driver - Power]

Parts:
C33, C35, C68: 1uF; C_0603_1608Metric
C34, C36, C37, C51, C53, C55, C65, C67: 100nF; C_0603_1608Metric
C38: 10nF/DNF; C_0603_1608Metric
C39, C40, C57, C64: 100uF/63V; CP_Radial_D8.0mm_P3.50mm
C41, C42: 100nF/100V; C_0603_1608Metric
C43: 1000uF/63V; CP_Radial_D16.0mm_P7.50mm
C44, C45, C46, C47, C48, C49, C50: 1nF/DNF; C_0603_1608Metric
C52, C54, C56, C66: 10uF; C_0603_1608Metric
C58: 22uF/35V; C_1210_3225Metric
C59: 100nF/35V; C_1206_3216Metric
C60: 470pF; C_0603_1608Metric
C61, C62: 100nF 10V; C_0603_1608Metric
C63: 22uF; C_0603_1608Metric
D1: SS510; D_SMA
D2: SS34; D_SMA
D3: 12V; D_SOD-123
D4, D5, D6, D7: Green; D_0603_1608Metric
F1: 5A; Fuse_Holder_1808_10.0mmx5mm
J3: 24V Power In; JST-XH-2P_SMD
L1, L4: 1uH 1.4A; L_0805_2012Metric
L2: 47uH/5A; L_47uH_4A_11mmx10mm_H4.8mm
L3: 1uH 4A; L_Taiyo-Yuden_MD-5050
L5: 220uH/2.1A; L_220uH_2A_15x15mm_H8mm
L6: 1uH/1.4A; L_0805_2012Metric
Q1, Q2: RU30L30; PDFN3333
R9: 100K; R_0603_1608Metric
R10, R12: 10K-DNF; R_0603_1608Metric
R11: 10K; R_0603_1608Metric
R13: R0.33; R_1206_3216Metric
R14, R18: 4.7K; R_0603_1608Metric
R15: 1.0K; R_0603_1608Metric
R16: 27K; R_0603_1608Metric
R17: 62K; R_0603_1608Metric
R19: 2.7K; R_0603_1608Metric
R20, R24: 100k; R_0603_1608Metric
R21: 130; R_0603_1608Metric
R22: 150R; R_0603_1608Metric
R23: 100*; R_0603_1608Metric
RV1: 100K; Potentiometer_Bourns_3266Y_Vertical
SW1: PWR SW C128955; SW_SMD_SPDT_PCM12_7.8x3.8
TP5, TP6, TP7, TP8, TP9, TP10, TP11, TP12: TestPoint; TestPoint_THTPad_1.5x1.5mm_Drill0.7mm
U17: ADC128S102CIMTX; TSSOP-16_4.4x5mm_P0.65mm
U18: HE6550MPR; SOT-89-3
U19: MC34063AD; SOIC-8_3.9x4.9mm_P1.27mm
U20: XC6227C331MR; SOT-23-5
U21: LM4040DIM3X-5; SOT-23
VR1: XL6019; DPAK170P1435X465-6N

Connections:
+3V3: C37.2, C65.1, C66.1, R19.1, TP8.1, U17.13 (Vd+), U20.5 (VOUT); also elsewhere on the board
+5V: C51.1, C52.1, L4.2, R18.1, TP6.1; also elsewhere on the board
+6V: C33.1, C34.1, C55.1, C56.1, C61.1, C64.1, C67.1, C68.1, L1.2, L6.1, U18.3 (VI), U20.1 (VIN), U20.3 (CE)
+24V: C39.1, C40.1, C41.1, C57.1, C58.1, C59.1, L2.2, Q2.3 (D), R13.1, R16.1, U19.6 (Vin), VR1.2 (EN), VR1.4 (VIN)
+VSW: L3.1, R9.2, R17.1, TP5.1; also elsewhere on the board
CS: U17.1 (~CS); also elsewhere on the board
GND: C33.2, C34.2, C35.2, C36.2, C37.1, C38.2, C39.2, C40.2, C41.2, C42.2, C43.2, C44.2, C45.2, C46.2, C47.2, C48.2, C49.2, C50.2, C51.2, C52.2, C53.2, C54.2, C55.2, C56.2, C57.2, C58.2, C59.2, C60.2, C61.2, C62.2, C63.2, C64.2, C65.2, C66.2, C67.2, C68.2, D2.2 (A), D4.1 (K), D5.1 (K), D6.1 (K), D7.1 (K), J3.1, R11.1, R12.1, R15.2, R20.2, RV1.1, TP10.1, U17.3 (AGND), U17.12 (DGND), U18.1 (GND), U19.4 (GND), U20.2 (GND), U21.2 (A), VR1.1 (GND); also elsewhere on the board
MISO: U17.15 (MISO); also elsewhere on the board
MOSI: U17.14 (MOSI); also elsewhere on the board
NR1: C44.1, U17.5 (IN1); also elsewhere on the board
NR2: C48.1, U17.6 (IN2); also elsewhere on the board
NR3: C45.1, U17.7 (IN3); also elsewhere on the board
NR4: C49.1, U17.8 (IN4); also elsewhere on the board
NR5: C46.1, U17.9 (IN5); also elsewhere on the board
NR6: C50.1, U17.10 (IN6); also elsewhere on the board
NR7: C47.1, U17.11 (IN7); also elsewhere on the board
unnamed: C35.1, L1.1, R21.1
unnamed: C36.1, R21.2, TP12.1, U17.2 (Va+), U21.1 (K)
unnamed: C38.1, R23.2, U17.4 (IN0)
unnamed: C42.1, C43.1, D1.1 (K), L3.2, R10.2, RV1.3
unnamed: C53.1, C54.1, L4.1, U18.2 (VO)
unnamed: C60.1, U19.3 (TC)
unnamed: C62.1, C63.1, L5.1, L6.2, R14.1, TP7.1
unnamed: D1.2 (A), L2.1, VR1.3 (SW), VR1.6 (SW)
unnamed: D2.1 (K), L5.2, U19.2 (SwE)
unnamed: D3.1 (K), Q1.1 (S), Q2.1 (S), R24.2
unnamed: D3.2 (A), Q1.2 (G), R20.1, SW1.1
unnamed: D4.2 (A), R16.2
unnamed: D5.2 (A), R17.2
unnamed: D6.2 (A), R18.2
unnamed: D7.2 (A), R19.2
unnamed: F1.1, J3.2, TP9.1
unnamed: F1.2, Q1.3 (D)
unnamed: Q2.2 (G), SW1.2
unnamed: R10.1, R12.2, RV1.2, VR1.5 (FB)
unnamed: R13.2, U19.1 (SwC), U19.7 (Ipk), U19.8 (DC)
unnamed: R14.2, R22.1, U19.5 (Vfb)
unnamed: R15.1, R22.2
unnamed: R24.1, SW1.3
SLCK: U17.16 (SCLK); also elsewhere on the board
VSW_Divider: R9.1, R11.2, R23.1, TP11.1

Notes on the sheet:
24V to 6V Buck converter
Drives the ESP32 + Sensors
Start with the Pot, but later can add in fixed voltage resistors
Power Supply LEDs
Switched 24V Power input + Reverse Polarity Protection
@700mA
45V = 4.091V 40V = 3.636V 35V = 3.182V 30V = 2.727V 24V = 2.182V
@150mA
5V and 3.3V LDO Regulators
8 Channel 5V ADC
24V Boost to 25V-40V @ 4A Converter
188KHz PWM Freq
100KHz PWM Freq
* 1nF filter caps might need to be larger? Add 100 ohm resistors in series?
6.237V @1.2A
(when R15+R22 = 1200 Ohm)
Vout = 1.25 * (1+(R15+R22)/R14)
OFF

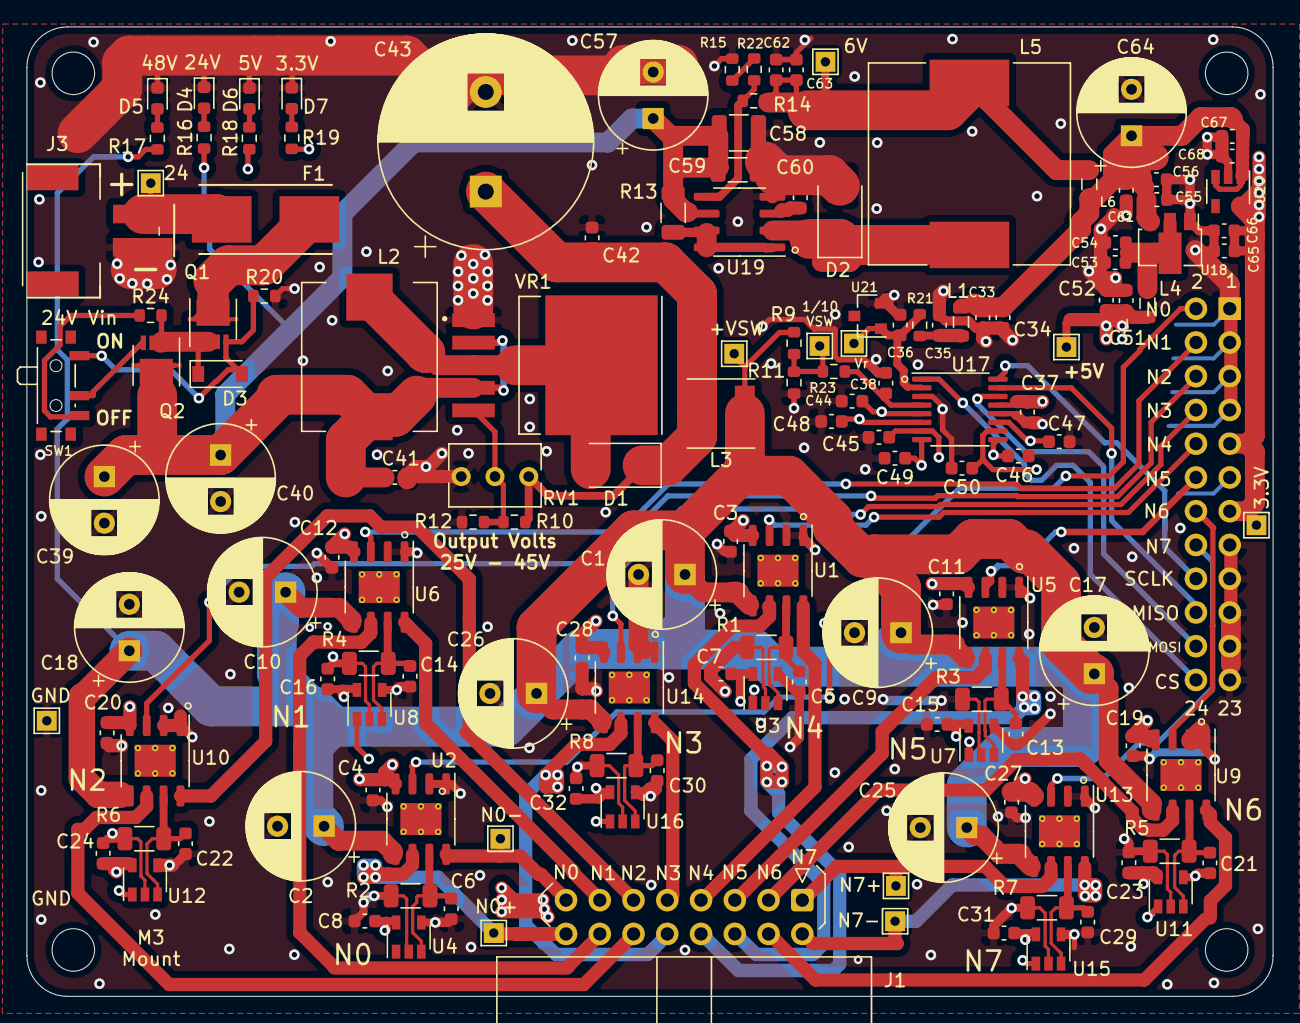
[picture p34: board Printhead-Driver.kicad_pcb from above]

Board: 4 copper layers, 93.8 x 73.0 mm, 151 parts (1 on the bottom side), 73 nets.

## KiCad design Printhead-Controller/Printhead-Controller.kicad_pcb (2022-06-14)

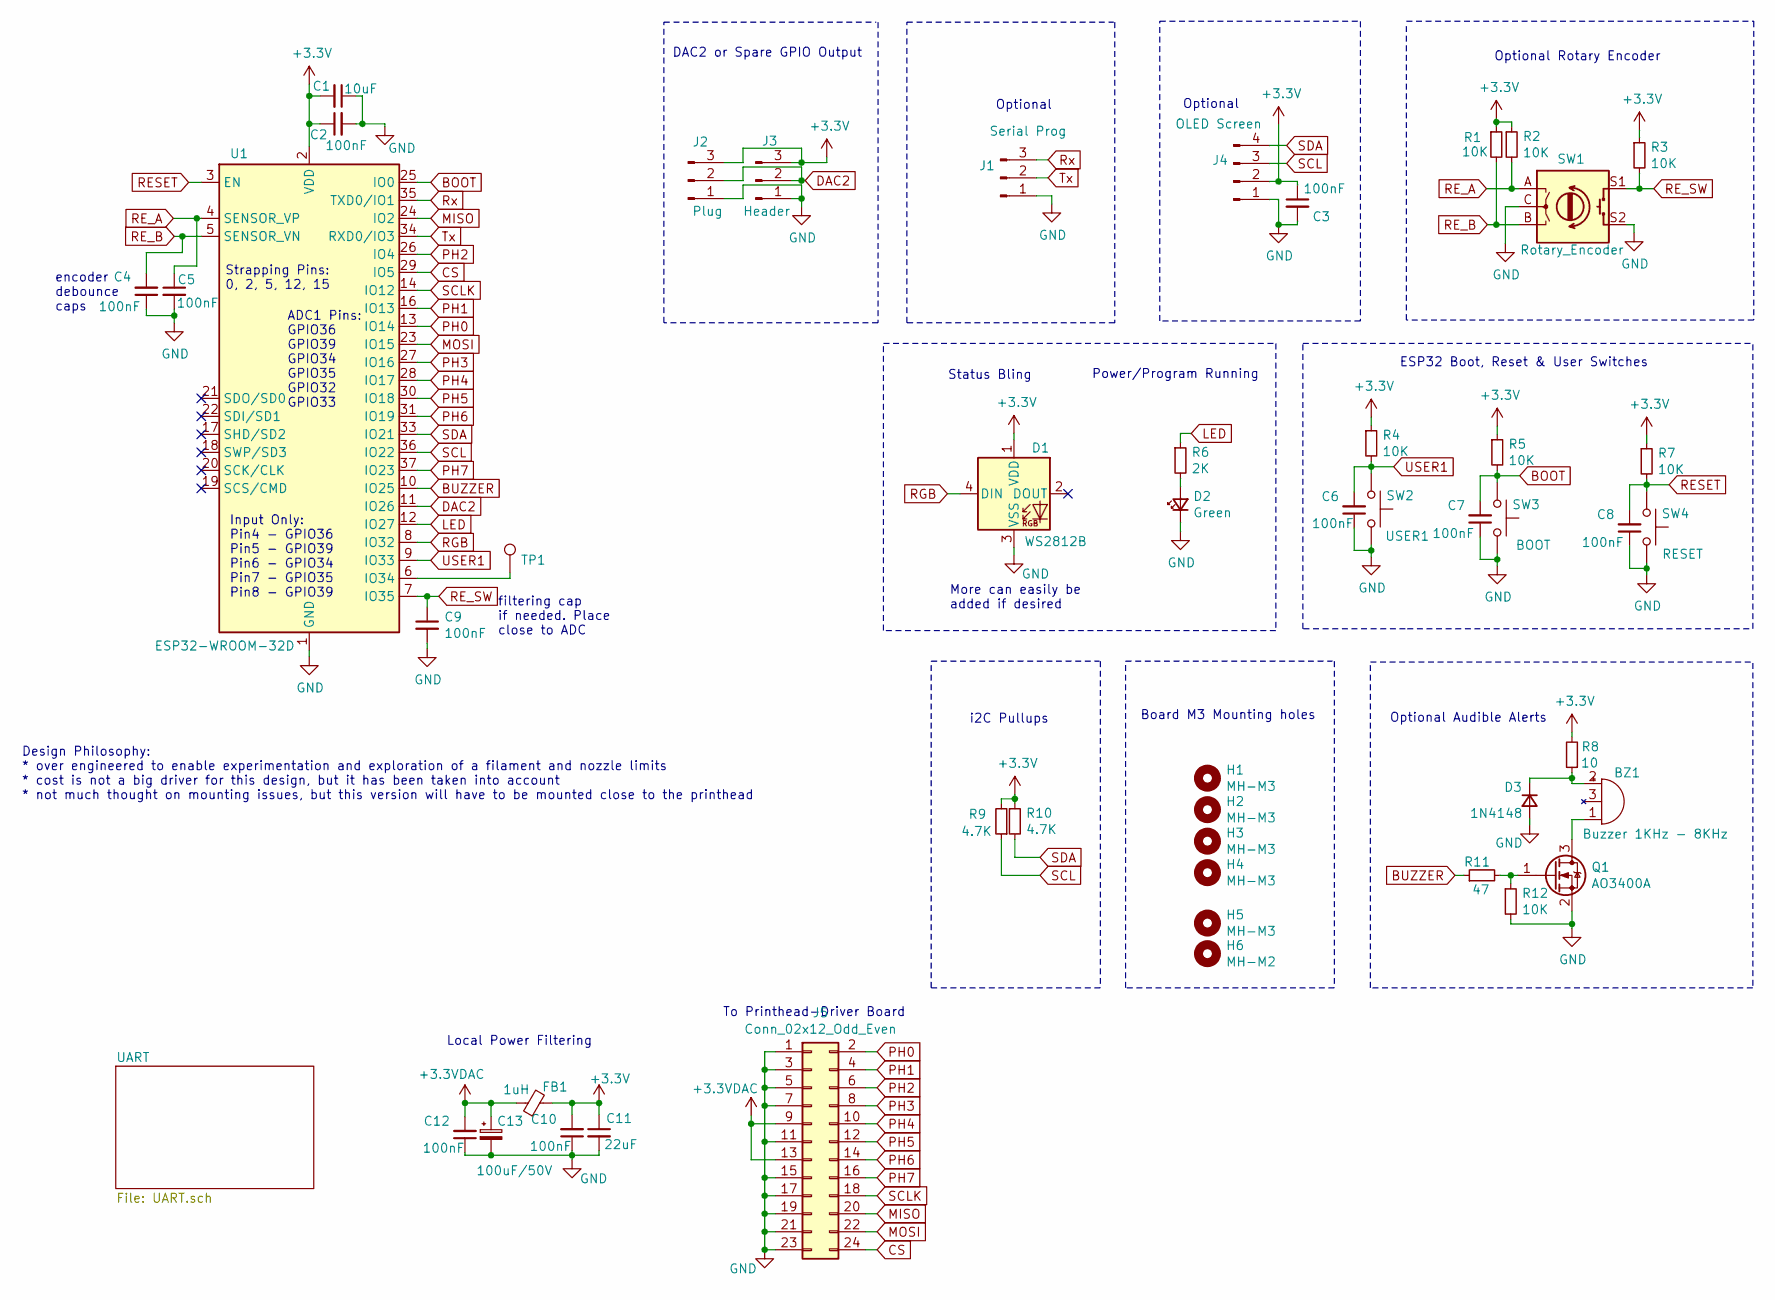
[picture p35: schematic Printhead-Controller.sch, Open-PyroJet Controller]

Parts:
BZ1: Buzzer 1KHz - 8KHz; MagneticBuzzer_5.2x5.2_4KHz
C1: 10uF; C_0603_1608Metric
C2, C3, C4, C5, C6, C7, C8, C9, C10, C12: 100nF; C_0603_1608Metric
C11: 22uF; C_0603_1608Metric
C13: 100uF/50V; CP_Radial_D8.0mm_P3.50mm
D1: WS2812B; LED_WS2812B_PLCC4_5.0x5.0mm_P3.2mm
D2: Green; LED_0603_1608Metric
D3: 1N4148; D_0805_2012Metric
FB1: 1uH; R_0805_2012Metric
H1, H2, H3, H4, H5: MH-M3; MountingHole_3.2mm_M3
H6: MH-M2; MountingHole_2.2mm_M2
J1: Serial Prog; PinHeader_1x03_P1.27mm_Vertical
J2: Plug; Hirose_DF13C_CL535-0403-5-51_1x03-1MP_P1.25mm_Vertical
J3: Header; PinHeader_1x03_P2.54mm_Vertical
J4: OLED Screen; PinHeader_1x04_P2.54mm_Vertical
J5: Conn_02x12_Odd_Even; PinHeader_2x12_P2.54mm_Vertical
Q1: AO3400A; SOT-23
R1, R2, R3, R4, R5, R7, R12: 10K; R_0603_1608Metric
R6: 2K; R_0603_1608Metric
R8: 10; R_0805_2012Metric
R9, R10: 4.7K; R_0603_1608Metric
R11: 47; R_0603_1608Metric
SW1: Rotary_Encoder; RotaryEncoder_Alps_EC11E-Switch_Vertical_H20mm
SW2: USER1; SW_SMD_SPST_SKQG_WithStem_6x6.5
SW3: BOOT; SMD_Switch_5x3
SW4: RESET; SMD_Switch_5x3
TP1: TestPoint; TestPoint_THTPad_1.5x1.5mm_Drill0.7mm
U1: ESP32-WROOM-32D; ESP32-WROOM-32

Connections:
+3.3VDAC: C12.2, C13.1, FB1.1, J5.9, J5.13
BOOT: C7.2, R5.2, SW3.1, U1.25 (IO0); also elsewhere on the board
BUZZER: R11.1, U1.10 (IO25)
CS: J5.24, U1.29 (IO5)
DAC2: J2.2, J3.2, U1.11 (IO26)
GND: C1.1, C2.2, C3.2, C4.1, C5.2, C6.1, C7.1, C8.1, C9.2, C10.1, C11.2, C12.1, C13.2, D1.3 (VSS), D2.1 (K), D3.2 (A), J1.1, J2.1, J3.1, J4.1, J5.1, J5.3, J5.5, J5.7, J5.11, J5.15, J5.17, J5.19, J5.21, J5.23, Q1.2 (S), R12.2, SW1.C, SW1.S2, SW2.2, SW3.2, SW4.2, U1.1 (GND), U1.15 (GND), U1.38 (GND), U1.39 (GND); also elsewhere on the board
LED: R6.1, U1.12 (IO27)
MISO: J5.20, U1.24 (IO2)
MOSI: J5.22, U1.23 (IO15)
unnamed: BZ1.1 (-), Q1.3 (D)
unnamed: BZ1.2 (+), D3.1 (K), R8.1
unnamed: D2.2 (A), R6.2
unnamed: Q1.1 (G), R11.2, R12.1
unnamed: TP1.1, U1.6 (IO34)
PH0: J5.2, U1.13 (IO14)
PH1: J5.4, U1.16 (IO13)
PH2: J5.6, U1.26 (IO4)
PH3: J5.8, U1.27 (IO16)
PH4: J5.10, U1.28 (IO17)
PH5: J5.12, U1.30 (IO18)
PH6: J5.14, U1.31 (IO19)
PH7: J5.16, U1.37 (IO23)
RESET: C8.2, R7.2, SW4.1, U1.3 (EN); also elsewhere on the board
RE_A: C5.1, R2.2, SW1.A, U1.4 (SENSOR_VP)
RE_B: C4.2, R1.2, SW1.B, U1.5 (SENSOR_VN)
RE_SW: C9.1, R3.2, SW1.S1, U1.7 (IO35)
RGB: D1.4 (DIN), U1.8 (IO32)
Rx: J1.3, U1.35 (TXD0/IO1); also elsewhere on the board
SCL: J4.3, R9.1, U1.36 (IO22)
SCLK: J5.18, U1.14 (IO12)
SDA: J4.4, R10.2, U1.33 (IO21)
Tx: J1.2, U1.34 (RXD0/IO3); also elsewhere on the board
USER1: C6.2, R4.2, SW2.1, U1.9 (IO33)

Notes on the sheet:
Input Only: Pin4 - GPIO36 Pin5 - GPIO39 Pin6 - GPIO34 Pin7 - GPIO35 Pin8 - GPIO39
Strapping Pins: 0, 2, 5, 12, 15
ADC1 Pins: GPIO36 GPIO39 GPIO34 GPIO35 GPIO32 GPIO33
Optional
Optional Rotary Encoder
ESP32 Boot, Reset & User Switches
Power/Program Running
Status Bling
More can easily be added if desired
Design Philosophy: * over engineered to enable experimentation and exploration of a filament and nozzle limits * cost is not a big driver for this design, but it has been taken into account * not much thought on mounting issues, but this version will have to be mounted close to the printhead
Optional Audible Alerts
encoder debounce caps
Board M3 Mounting holes
filtering cap if needed. Place close to ADC
To Printhead-Driver Board
i2C Pullups
Local Power Filtering
DAC2 or Spare GPIO Output

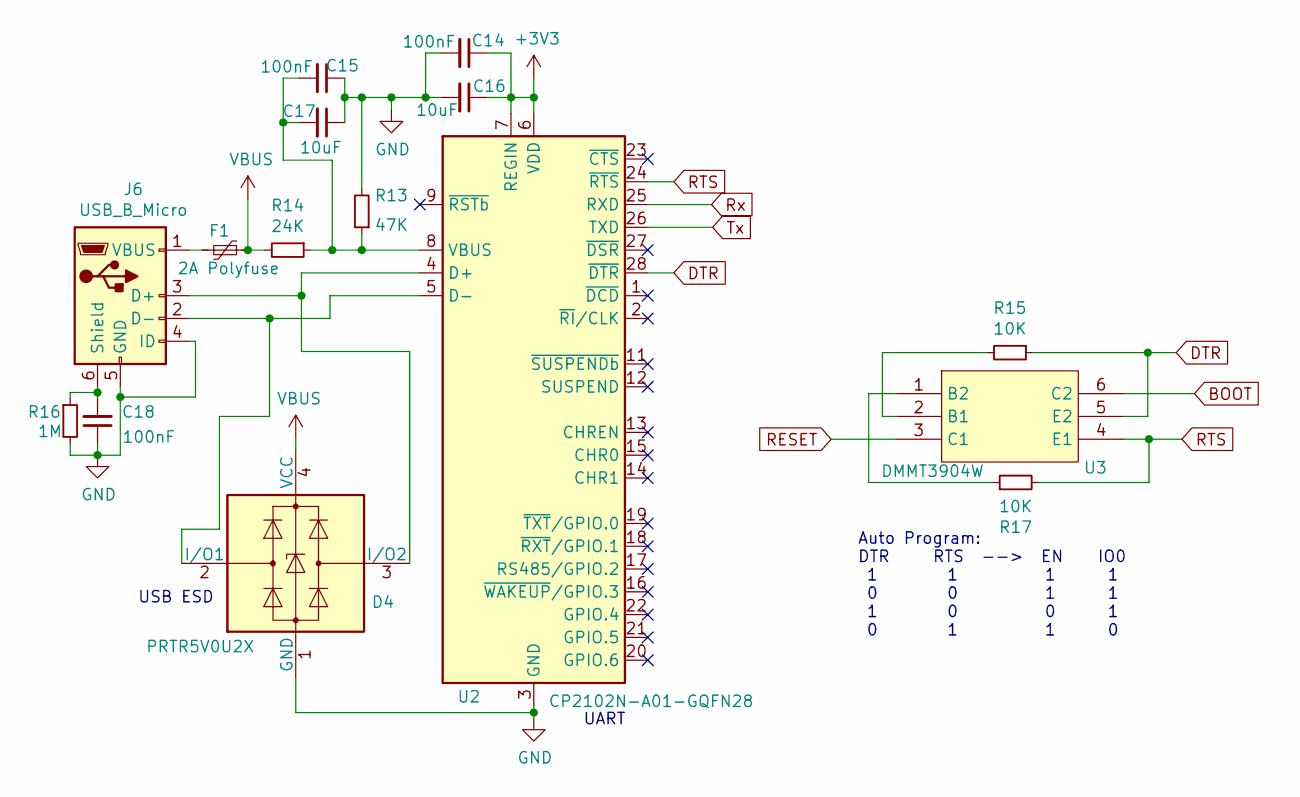
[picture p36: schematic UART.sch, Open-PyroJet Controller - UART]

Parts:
C14, C15, C18: 100nF; C_0603_1608Metric
C16, C17: 10uF; C_0603_1608Metric
D4: PRTR5V0U2X; SOT-143
F1: 2A Polyfuse; C_0805_2012Metric
J6: USB_B_Micro; USB_Micro-B_C319160
R13: 47K; R_0603_1608Metric
R14: 24K; R_0603_1608Metric
R15, R17: 10K; R_0603_1608Metric
R16: 1M; R_0603_1608Metric
U2: CP2102N-A01-GQFN28; QFN-28-1EP_5x5mm_P0.5mm_EP3.35x3.35mm
U3: DMMT3904W; SOT-363_SC-70-6

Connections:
BOOT: U3.6 (C2); also elsewhere on the board
DTR: R15.1, U2.28 (~DTR), U3.5 (E2)
GND: C14.2, C15.1, C16.2, C17.1, C18.1, D4.1 (GND), J6.4 (ID), J6.5 (GND), R13.2, R16.2, U2.3 (GND), U2.29 (GND); also elsewhere on the board
unnamed: C15.2, C17.2, R13.1, R14.1, U2.8 (VBUS)
unnamed: C18.2, J6.6 (Shield), R16.1
unnamed: D4.2 (I/O1), J6.2 (D-), U2.5 (D-)
unnamed: D4.3 (I/O2), J6.3 (D+), U2.4 (D+)
unnamed: F1.2, J6.1 (VBUS)
unnamed: R15.2, U3.2 (B1)
unnamed: R17.1, U3.1 (B2)
RESET: U3.3 (C1); also elsewhere on the board
RTS: R17.2, U2.24 (~RTS), U3.4 (E1)
Rx: U2.25 (RXD); also elsewhere on the board
Tx: U2.26 (TXD); also elsewhere on the board
VBUS: D4.4 (VCC), F1.1, R14.2

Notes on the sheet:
Auto Program: DTR RTS --> EN IO0 1 1 1 1 0 0 1 1 1 0 0 1 0 1 1 0
USB ESD
UART

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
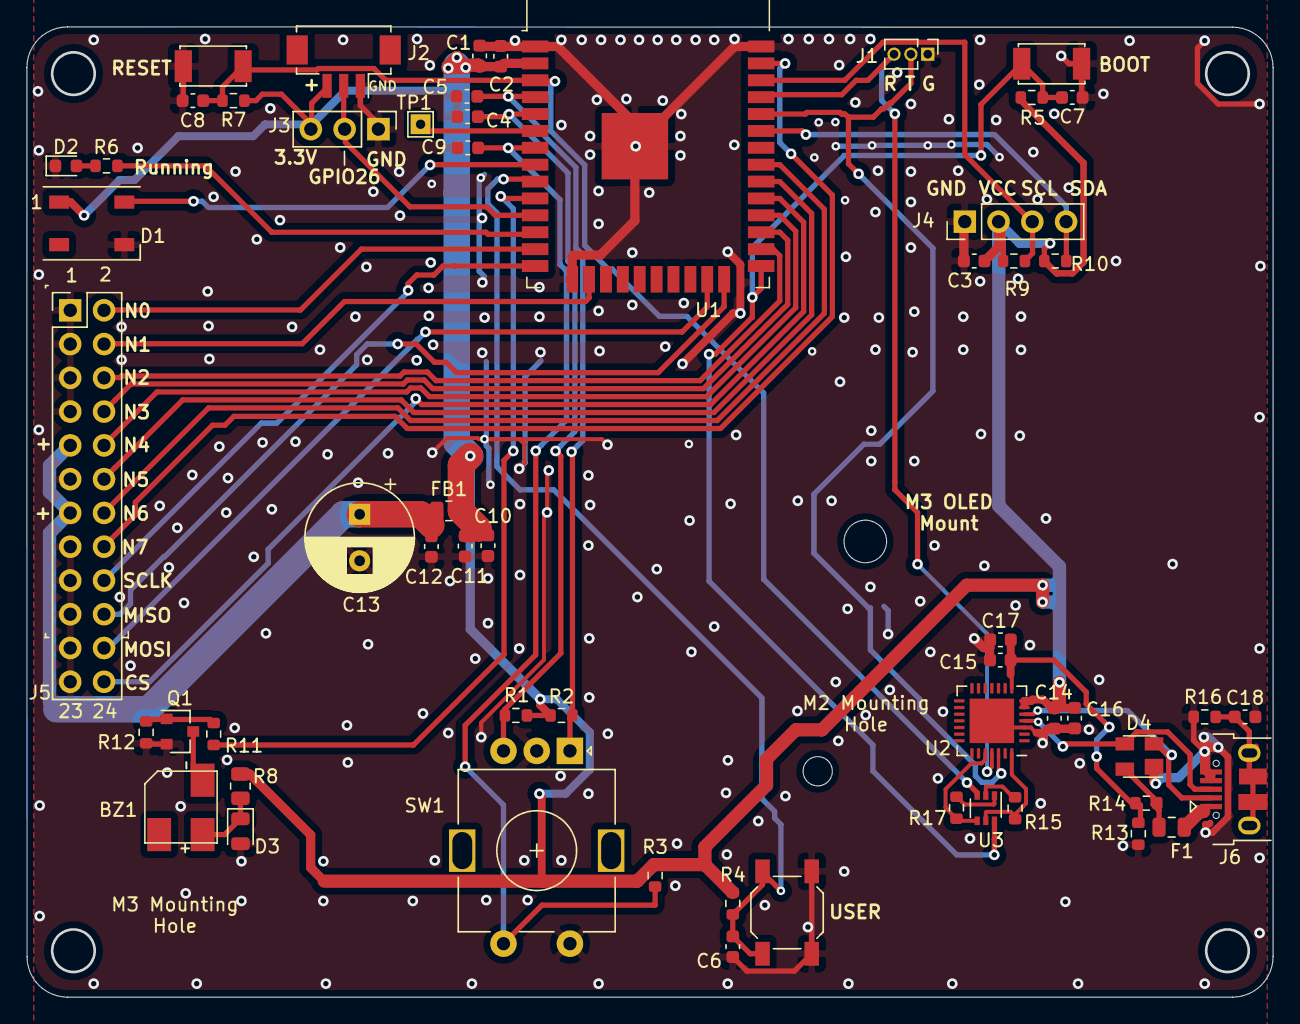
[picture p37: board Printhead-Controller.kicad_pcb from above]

Board: 2 copper layers, 93.7 x 73.0 mm, 63 parts (0 on the bottom side), 44 nets.

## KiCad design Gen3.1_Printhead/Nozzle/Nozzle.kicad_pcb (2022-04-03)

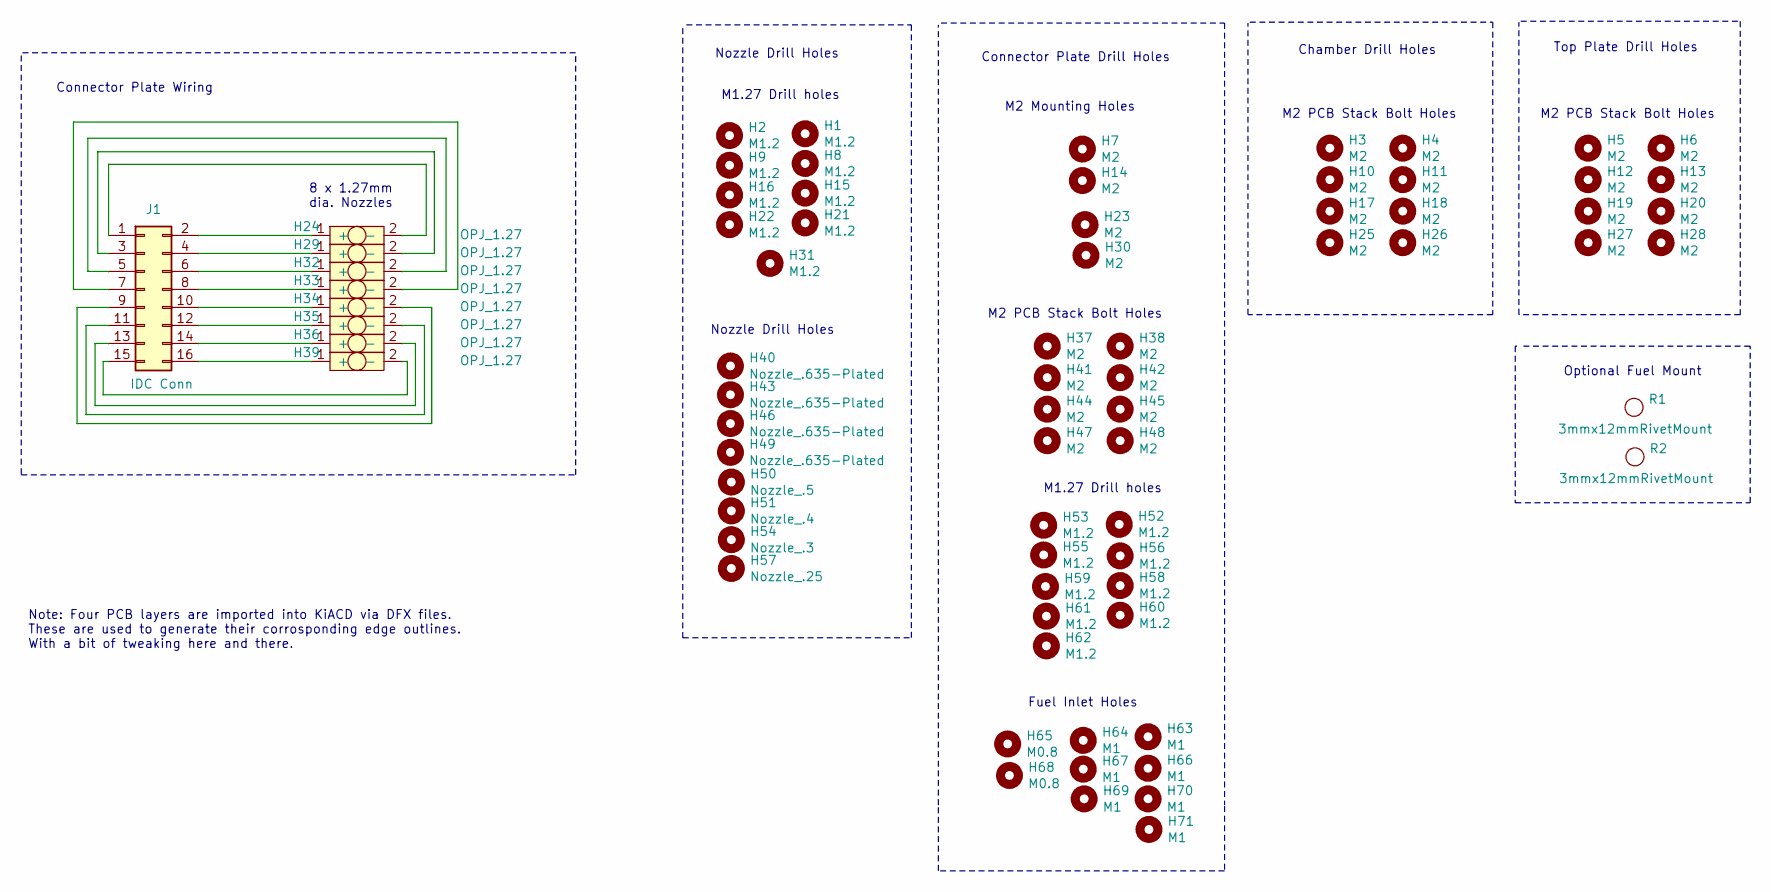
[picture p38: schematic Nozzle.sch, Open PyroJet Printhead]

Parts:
H1, H2, H8, H9, H15, H16, H21, H22, H31, H52, H53, H55, H56, H58, H59, H60, H61, H62: M1.2; MountingHole_1.2mm
H3, H4, H5, H6, H7, H10, H11, H12, H13, H14, H17, H18, H19, H20, H23, H25, H26, H27, H28, H30, H37, H38, H41, H42, H44, H45, H47, H48: M2; MountingHole_2.2mm_M2
H24, H29, H32, H33, H34, H35, H36, H39: OPJ_1.27
H40, H43, H46, H49: Nozzle_.635-Plated; Nozzle_0.635-Plated
H50: Nozzle_.5; Nozzle_0.5
H51: Nozzle_.4; Nozzle_0.4
H54: Nozzle_.3; Nozzle_0.3
H57: Nozzle_.25; Nozzle_0.25
H63, H64, H66, H67, H69, H70, H71: M1; MountingHole_1mm
H65, H68: M0.8; MountingHole_0.8mm
J1: IDC Conn; PinSocket_2x08_P2.54mm_Vertical
R1, R2: 3mmx12mmRivetMount; 3mmx12mmHollowRivet

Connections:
unnamed: H24.1 (+), J1.2
unnamed: H24.2 (-), J1.1
unnamed: H29.1 (+), J1.4
unnamed: H29.2 (-), J1.3
unnamed: H32.1 (+), J1.6
unnamed: H32.2 (-), J1.5
unnamed: H33.1 (+), J1.8
unnamed: H33.2 (-), J1.7
unnamed: H34.1 (+), J1.10
unnamed: H34.2 (-), J1.9
unnamed: H35.1 (+), J1.12
unnamed: H35.2 (-), J1.11
unnamed: H36.1 (+), J1.14
unnamed: H36.2 (-), J1.13
unnamed: H39.1 (+), J1.16
unnamed: H39.2 (-), J1.15

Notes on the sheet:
8 x 1.27mm dia. Nozzles
Optional Fuel Mount
M2 Mounting Holes
Connector Plate Wiring
Note: Four PCB layers are imported into KiACD via DFX files. These are used to generate their corrosponding edge outlines. With a bit of tweaking here and there.
M2 PCB Stack Bolt Holes
M1.27 Drill holes
Connector Plate Drill Holes
Nozzle Drill Holes
Chamber Drill Holes
Top Plate Drill Holes
Fuel Inlet Holes

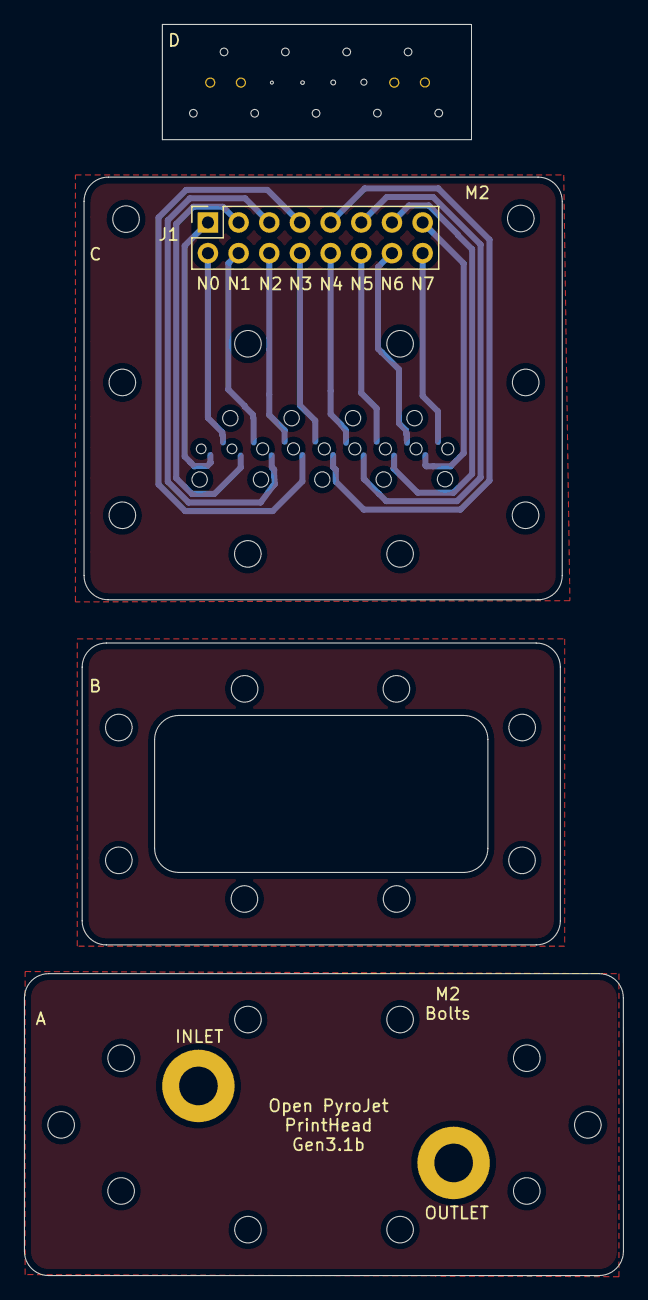
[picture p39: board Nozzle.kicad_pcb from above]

Board: 2 copper layers, 49.6 x 103.6 mm, 74 parts (0 on the bottom side), 16 nets.

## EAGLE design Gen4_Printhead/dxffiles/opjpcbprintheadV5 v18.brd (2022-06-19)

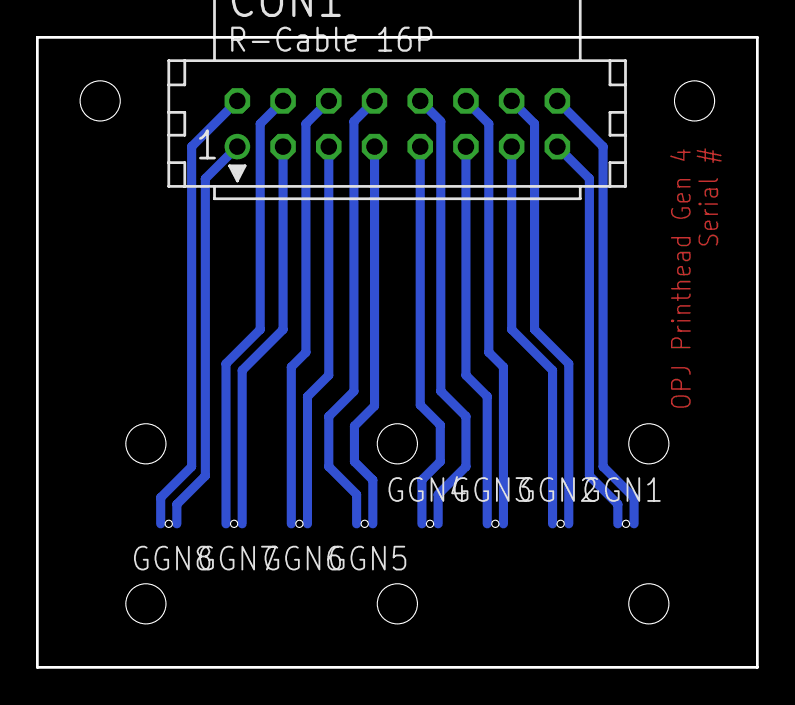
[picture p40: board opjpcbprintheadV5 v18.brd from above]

Board: 2 copper layers, 40.0 x 35.0 mm, 9 parts (0 on the bottom side), 16 nets.

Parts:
CON1: CON16
GGN1, GGN2, GGN3, GGN4, GGN5, GGN6, GGN7, GGN8: OPJGASGUN

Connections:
unnamed: CON1.1, GGN8.VCC
unnamed: CON1.3, GGN7.VCC
unnamed: CON1.5, GGN6.VCC
unnamed: CON1.7, GGN5.VCC
unnamed: CON1.9, GGN4.VCC
unnamed: CON1.11, GGN3.VCC
unnamed: CON1.13, GGN2.VCC
unnamed: CON1.15, GGN1.VCC
unnamed: CON1.16, GGN1.GND
unnamed: CON1.2, GGN8.GND
unnamed: CON1.4, GGN7.GND
unnamed: CON1.6, GGN6.GND
unnamed: CON1.8, GGN5.GND
unnamed: CON1.14, GGN2.GND
unnamed: CON1.12, GGN3.GND
unnamed: CON1.10, GGN4.GND

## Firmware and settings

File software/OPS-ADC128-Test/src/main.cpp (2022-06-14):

/* #####################################
*
* an example Test program for the OPJ_V0.6 set of boards to select pulse length and nozzle number
* then fire the nozzle
*
* Parkview 2022-04-24 (I am NOT a software guy)
* MIT License - Open Source Software
*
* See: https://github.com/Sindry-Manufacturing/OpenPyrojet-Jetpack  ; for much more complete software solution
*
List of todo's:
  * TODO: change Rotary Encoder over to proper number tracking!
  * TODO: setup power LED with PWM so we can adjust brightness
  * TODO: add in ADC routine to record VSW current usage during
      firing a nozzle.
  * TODO: Be great to show the data as a graph on the OLED screen
  * DONE: get menu working correctly on screen
  * DONE: get nozzles firing with set paramemters
*/

#include <Arduino.h>
#include <Wire.h>
#include "SSD1306Wire.h"
#include "FastLED.h"
#include "AiEsp32RotaryEncoder.h"
#include "spi.h"
#include "main.h"

#define OLED_DISPLAY true    // Enable OLED Display
#define OLED_DISPLAY_SSD1306 // OLED Display Type: SSD1306(OLED_DISPLAY_SSD1306) / SH1106(OLED_DISPLAY_SH1106), comment this line out to disable oled
#define numRGBLED 1          // number of RGB LEDs to light up
#define BRIGHTNESS 78        // Control the brightness of RGB led(s)
#define SATURATION 255       // Control the saturation of RGB led(s)
#define LED_TYPE WS2812      // type of RGB LED
#define RGBLEDPin 32         // GPIO that the WS2812 RGB LED is on
#define COLOR_ORDER GRB
#define PowerLEDPin 27 // GPIO of the Power LED D1
#define WAIT 300       // delay loop sleep time
#define buzzerPin 25   // Buzzer GPIO pin
#define userSWPin 26   // User switch GPIO pin
#define bootPin 0      // Boot switch GPIO pin
#define ROTARY_ENCODER_BUTTON_PIN 35
#define ROTARY_ENCODER_A_PIN 39
#define ROTARY_ENCODER_B_PIN 36
#define ROTARY_ENCODER_STEPS 4    // 1, 2, 4 steps per rotary step bump
#define ROTARY_ENCODER_VCC_PIN -1 // Encoder is connected direct to VCC
#define nozzle0 14
#define nozzle1 13
#define nozzle2 4
#define nozzle3 16
#define nozzle4 17
#define nozzle5 18
#define nozzle6 19
#define nozzle7 23
#define HSPI_CS 5
#define HSPI_MOSI 15
#define HSPI_MISO 2
#define HSPI_SCLK 12
int nozzles[8] = {14, 13, 4, 16, 17, 18, 19, 23}; // list of nozzle GPIO firing pins
#define powerLEDbrightness 50                     // set Green Power LED to 50% brightness
#define ADC121Addr 0x51                           // equiv: 0x51 or 81D  Tested via i2CScanner

const uint32_t FREQ = 400000;      // i2C clock Frequencies: 100000; 400000; 1700000; 3400000
const uint8_t I2C_SDA_PIN = 21;    // ESP32 WROOM32 i2c SDA Pin
const uint8_t I2C_SCL_PIN = 22;    // ESP32 WROOM32 i2c SCL Pin
const uint8_t DISPLAY_WIDTH = 128; // OLED display pixel width
const uint8_t DISPLAY_HEIGHT = 64; // OLED display pixel height
bool ledMode = 0;
bool circleValues = false; // circle around rotary encoder or not
// bool circleValues = true;  // circle around rotary encoder or not
uint8_t menuState = 1;             // entry state of the menuState machine
uint8_t nozzleNumber = 1;          // current nozzle number selected
uint8_t pulseLength = 1;           // current pulse length in miliSeconds
static const int spiClk = 12000000; // Min is 8MHz, Max is 16MHz

SPIClass *hspi = NULL;

CRGB leds[numRGBLED];

AiEsp32RotaryEncoder rotaryEncoder = AiEsp32RotaryEncoder(ROTARY_ENCODER_A_PIN, ROTARY_ENCODER_B_PIN, ROTARY_ENCODER_BUTTON_PIN, ROTARY_ENCODER_VCC_PIN, ROTARY_ENCODER_STEPS);


#ifdef OLED_DISPLAY_SSD1306
SSD1306Wire display(0x3c, I2C_SDA_PIN, I2C_SCL_PIN);
#endif

/**
 * Generic I2C Read function
 *
 * @param devAddr I2C Device address
 * @param reg Register address
 * @param val pointer to byte array to read into
 * @param length number of bytes to read
 *
 * @return 0 on success, other on failure
 */

int readADC(int chan)
{
  // Reads from ADC128S102 8 channel ADC IC
  digitalWrite(SS, LOW);
  int hi = SPI.transfer(chan << 3);
  int lo = SPI.transfer(0);
  digitalWrite(SS, HIGH);

  return (hi << 8) | lo;
}

int readFromRegAddr(uint8_t devAddr, uint8_t reg, void *val, size_t length)
// int readFromRegAddr(uint8_t devAddr, uint8_t reg, void *val, size_t length)
// int readFromRegAddr(uint8_t devAddr, uint8_t reg, void *val, size_t length, endian_e endianness)
{
  //  list out variables that have been passed to function:
  uint8_t *byteArray = (uint8_t *)val;
  int ret;
  int readData = 1;
  uint32_t i2cFreq = 0;
  Wire.beginTransmission(devAddr); // select the ADC121 IC
  if (Wire.write(reg) < 1)         // select the conversion register: 0
  {
    Serial.println("RETURN -1");
    return -1;
  }
  if ((ret = Wire.endTransmission(false)) != 0)
  {
    Serial.println("RETURN RET");
    return ret;
  }
  if (byteArray == NULL || length == 0)
  {
    Serial.println("RETURN 0");
    return 0;
  }
  digitalWrite(33, 1); // reading data, so pulse scope Sync GPIO: 33
  Wire.requestFrom(devAddr, (uint8_t)length);
  while (Wire.available() > 0 && readData < length)
  {
    byteArray[readData] = Wire.read();
    // byteArray[endianness == BIG_ENDIAN ? readData : length - 1 - readData] = Wire.read();
    readData--;
  }
  digitalWrite(33, 0); // finished reading data, turn off pulse scope Sync GPIO:33
  if ((ret = Wire.endTransmission(true)) != 0)
  {
    return ret;
  }
  return 0;
}

/**
 * Generic I2C Write function
 *
 * @param devAddr I2C Device address
 * @param reg Register address
 * @param val pointer to byte array to write from
 * @param length number of bytes to write
 *
 * @return 0 on success, other on failure
 */

int writeToRegAddr(uint8_t devAddr, uint8_t reg, void *val, size_t length)
// int writeToRegAddr(uint8_t devAddr, uint8_t reg, void *val, size_t length, endian_e endianness)
{
  uint8_t *byteArray = (uint8_t *)val;
  int ret;
  Wire.beginTransmission(devAddr);
  if (Wire.write(reg) < 1)
  {
    return -1;
  }
  for (int i = 0; i < length; i++)
  {
    if (Wire.write(byteArray[i]) < 1)
    {
      // if (Wire.write(byteArray[endianness == 0 ? i : length - 1 - i]) < 1) {
      return -1;
    }
  }
  if ((ret = Wire.endTransmission()) != 0)
  {
    return ret;
  }
  return 0;
}

void blinkPowerLED()
{
  // blink the Green Power/User LEDs
  // should change this over to ledc routine, so we can control the brightness
  digitalWrite(PowerLEDPin, LOW);
  delay(WAIT);
  digitalWrite(PowerLEDPin, HIGH);
}

void SoundBuzzer()
{
  //  sound the buzzer
  ledcWrite(0, 127); // turn on buzzer
  // Serial.println("Buzzer On");
  delay(WAIT);
  // Serial.println("Buzzer Off");
  ledcWrite(0, 0); // turn buzzer off
}

void blinkRGB()
{
  // cycle the WS2812 RGB LEDS to show they are all working ok
  // Serial.println("Cycle RGB LEDs On");
  leds[0] = CRGB::Red;
  FastLED.show();
  delay(300);
  leds[0] = CRGB::Green;
  FastLED.show();
  delay(300);
  leds[0] = CRGB::Blue;
  FastLED.show();
  delay(300);
  // Serial.println("RGB LEDs Off");
  leds[0] = CRGB::Black;
  FastLED.show();
}

void OLED_Header()
{
  // add a 1 line header to the OLED screen.
  display.clear();
  display.setTextAlignment(TEXT_ALIGN_LEFT);
  display.drawString(0, 0, "OpenPryoJet");
  display.drawLine(0, 12, DISPLAY_WIDTH, 12);
  // display.setTextAlignment(TEXT_ALIGN_RIGHT);
  display.setTextAlignment(TEXT_ALIGN_LEFT);
  display.display();
}

void displayText(int line, char *textline)
{
  // update menu with new data, Line one starts 12 pixels down
  display.clear();
  OLED_Header();
  display.drawString(2, line * 12, textline);
  delay(300);
  display.display();
}

void rotary_onButtonClick()
{
  static unsigned long lastTimePressed = 0;
  char msg[14];
  int Hue = 0;
  if (millis() - lastTimePressed < 200)
    return;
  lastTimePressed = millis();
  Hue = rotaryEncoder.readEncoder();
  Serial.print("Selected value is ");
  Serial.println(Hue, 1);
  sprintf(msg, "Encoder: %3d", Hue);
  displayText(30, msg);
  // Serial.print(numberSelector.getValue(), 1);
  Serial.println(" ***********************");
}

void rotary_loop()
{
  // dont print anything unless value changed
  if (!rotaryEncoder.encoderChanged())
  {
    Serial.println(rotaryEncoder.readEncoder());
    return;
  }
  Serial.print("Value: ");
  Serial.println(rotaryEncoder.readEncoder());
}

void IRAM_ATTR readEncoderISR()
{
  rotaryEncoder.readEncoder_ISR();
}

// Read value from converter
float read_current()
{
  uint16_t raw = 0;
  readFromRegAddr(ADC121Addr, ADC121_CONV_REG, &raw, 2);
  // Wire.setClock(100000);
  return ((float)raw) / ADC121_MAX_VAL * ADC121_REF_V;
  // return ((float)raw);
}

int spiCommand(SPIClass *spi, byte chan)
{
  // use it as you would the regular arduino SPI API
  uint16_t hiByte = 0;
  uint16_t loByte = 0;
  spi->beginTransaction(SPISettings(spiClk, MSBFIRST, SPI_MODE2));
  //digitalWrite(spi->pinSS(), LOW); // pull SS slow to prep other end for transfer
    uint32_t startTime = micros();
  digitalWrite(HSPI_CS, LOW); // pull ss high to signify end of data transfer
  //spi->transfer(0x00);
  hiByte = spi->transfer16((chan & 0x7) << 3);
//  loByte = spi->transfer(0);
  //digitalWrite(spi->pinSS(), HIGH); // pull ss high to signify end of data transfer
  digitalWrite(HSPI_CS, HIGH); // pull ss high to signify end of data transfer
    uint32_t endTime = micros();
  spi->endTransaction();
  //Serial.println("SPI done!");
    Serial.print("MicroSeconds to read sensor: ");
    Serial.println(endTime - startTime);

  return hiByte;
  return (hiByte << 8) | loByte;
}

void setup()
{
  // put your setup code here, to run once:
  ledcSetup(0, 4000, 8);
  ledcAttachPin(buzzerPin, 0);
  SoundBuzzer();
  pinMode(bootPin, INPUT);
  pinMode(userSWPin, INPUT);
  pinMode(PowerLEDPin, OUTPUT);
  pinMode(nozzle0, OUTPUT);
  pinMode(nozzle1, OUTPUT);
  pinMode(nozzle2, OUTPUT);
  pinMode(nozzle3, OUTPUT);
  pinMode(nozzle4, OUTPUT);
  pinMode(nozzle5, OUTPUT);
  pinMode(nozzle6, OUTPUT);
  pinMode(nozzle7, OUTPUT);
  pinMode(33, OUTPUT);
  digitalWrite(nozzle0, LOW);
  digitalWrite(nozzle1, LOW);
  digitalWrite(nozzle2, LOW);
  digitalWrite(nozzle3, LOW);
  digitalWrite(nozzle4, LOW);
  digitalWrite(nozzle5, LOW);
  digitalWrite(nozzle6, LOW);
  digitalWrite(nozzle7, LOW);
  digitalWrite(33, LOW);
  digitalWrite(PowerLEDPin, HIGH);
  blinkPowerLED();
  Serial.begin(115200);
  Serial.println("");
  Serial.println("Serial setup done!");
  Wire.begin(I2C_SDA_PIN, I2C_SCL_PIN, FREQ); //(SDA, SCL): uint8_t slaveAddr, int sda=-1, int scl=-1, uint32_t frequency=0
  Serial.println("Wire Begin done!");
  FastLED.addLeds<LED_TYPE, RGBLEDPin, COLOR_ORDER>(leds, numRGBLED).setCorrection(TypicalLEDStrip);
  FastLED.setBrightness(BRIGHTNESS);
  Serial.println("Fastwire finished done!");
  blinkRGB();
#if OLED_DISPLAY
  Serial.println("display init start!");
  display.init();
  Serial.println("display init finished done!");
  display.flipScreenVertically(); // setup depends on how the PCB is mounted
  display.setContrast(255);
  display.setFont(ArialMT_Plain_10);
  display.setColor(WHITE);
  display.setTextAlignment(TEXT_ALIGN_LEFT);
  display.drawLine(0, 12, DISPLAY_WIDTH, 12);
  display.display();
#endif
  OLED_Header();
  rotaryEncoder.begin();
  rotaryEncoder.setup(readEncoderISR);
  rotaryEncoder.setBoundaries(0, 255, circleValues); // minValue, maxValue, circleValues true|false (when max go to min and vice versa)
  rotaryEncoder.setEncoderValue(1);                  // set the starting number
  rotaryEncoder.setAcceleration(150);                // Acceleration 2-255; 0 or 1 disables Accel.

  // set RGB LED to State 1
  leds[0] = CHSV(96, 255, BRIGHTNESS); // set to Green
  FastLED.show();
  // init the ADC routines
  uint8_t buf = 0x00;
  buf = ADC121_CONFIG_CYCLE_32 & ADC121_CONFIG_CYCLE_MASK; // make sure to set Auto conversion
  Serial.println("Buffer: ");
  Serial.println(buf);
  writeToRegAddr(ADC121Addr, ADC121_CONFIG_REG, &buf, 1);
  //  ADC init finished

  Serial.println("ADC Setup completed!");
  Serial.print("Current: ");
  Serial.println(read_current());
  // setup for SPI ADC IC
  hspi = new SPIClass(HSPI);
  hspi->begin(HSPI_SCLK, HSPI_MISO, HSPI_MOSI, HSPI_CS); // SCLK, MISO, MOSI, SS
  pinMode(HSPI_CS, OUTPUT);                              // HSPI SS
  digitalWrite(HSPI_CS, HIGH); // pull ss high to signify end of data transfer
  // sound buzzer, to test and let people know setup has finished
  // SPI.setBitOrder();
  SoundBuzzer();
}

void loop()
{
  // put your main code here, to run repeatedly:
  // blinkRGB();
  float vRef = 4.825;  // ADC128 Reference Voltage.  This needs to be changed if you modify the PCB design
  float vADC = vRef/4096; // ADC segment
  uint8_t charPosition = 5;
  uint8_t reValue = 0;
  uint8_t LEDwarning = BRIGHTNESS + 50;
  // uint8_t chan = 0; // ADC128 port to read
  uint8_t chnl = 0;
  uint16_t data = 0;
  // CH: 0 = VSW; 1 = Nozzle 1; 2 = Nozzle2; ... 7 = Nozzle 7.  Note: Nozzle 0 does not have INA180, or ADC port.
  data = spiCommand(hspi, chnl);
  Serial.print("ADC: ");
  Serial.println(data * vADC);
  /*
  if (LEDwarning > 255)
  {
    LEDwarning = 255;
  }
  if ((menuState == 3) && (digitalRead(userSWPin) == LOW))
  {
    // fire current nozzle for set number of mSec
    blinkPowerLED();
    Serial.print("i2C Clock Speed: ");
    Serial.println(Wire.getClock());
    float curOneA = readADC(0);
    float curOneB = readADC(0);
    digitalWrite(nozzles[nozzleNumber], 1);
    delayMicroseconds(20);
    uint32_t startTime = micros();
    float curOne = readADC(0);
    uint32_t endTime = micros();
    float curTwo = readADC(0);
    float curThr = readADC(0);
    // Serial.println(read_current());
    delay(pulseLength);
    digitalWrite(nozzles[nozzleNumber], 0);
    delayMicroseconds(20);
    float curOneC = readADC(0);
    float curOneD = readADC(0);
    Serial.print("Current: ");
    Serial.println(curOneA);
    Serial.print("Current: ");
    Serial.println(curOneB);
    Serial.println("----");
    Serial.print("Current: ");
    Serial.println(curOne);
    Serial.print("Current: ");
    Serial.println(curTwo);
    Serial.print("Current: ");
    Serial.println(curThr);
    Serial.println("----");
    Serial.print("Current: ");
    Serial.println(curOneC);
    Serial.print("Current: ");
    Serial.println(curOneD);
    Serial.print("MicroSeconds to read sensor: ");
    Serial.println(endTime - startTime);
    SoundBuzzer();
    Serial.print("Just Fired Nozzle: ");
    Serial.print(nozzleNumber);
    Serial.print(" [");
    Serial.print(nozzles[nozzleNumber]);
    Serial.print("] for: ");
    Serial.print(pulseLength);
    Serial.println(" mSec!");
  }

  if (rotaryEncoder.encoderChanged())
  {
    // activate rotary encoder if its changed
    // ledMode = !ledMode;
    blinkPowerLED();
    reValue = rotaryEncoder.readEncoder();
    Serial.print("New RE Value: ");
    Serial.println(reValue);
    switch (menuState)
    {
    // update current menu value with new RE value
    case 1:
      // update Nozzle number 0-7
      nozzleNumber = reValue;
      if (nozzleNumber > 7)
      {
        nozzleNumber = 7;
      }
      else if (nozzleNumber < 0)
      {
        nozzleNumber = 0;
      }
      break;
    case 2:
      // update pulse Length value
      pulseLength = reValue;
      if (pulseLength > 20)
      {
        pulseLength = 20;
      }
      else if (pulseLength < 1)
      {
        pulseLength = 1;
      }
      break;
    case 3:
      // now set to fire current nozzle mode. Wait for User button press!
      break;
    }
  }
  if (rotaryEncoder.isEncoderButtonClicked())
  {
    Serial.println("RE switch pressed");
    // cycle around three menu states: 1) Nozzle #; 2) pulse length; 3) fire nozzle
    switch (menuState)
    {
    case 1:
      menuState = 2;
      leds[0] = CHSV(160, 255, BRIGHTNESS); // set to Blue
      FastLED.show();
      break;
    case 2:
      menuState = 3;
      leds[0] = CHSV(0, 255, LEDwarning); // set to RED
      FastLED.show();
      break;
    case 3:
      menuState = 1;
      leds[0] = CHSV(96, 255, BRIGHTNESS); // set to Green
      FastLED.show();
      break;
    }
    SoundBuzzer();
  }
  // update display to show new state and values
  OLED_Header();
  switch (menuState)
  {
  case 1:
    display.drawString(10, 1 * 12, "Nozzle No: ");
    display.drawString(13 * charPosition, 1 * 12, String(nozzleNumber));
    display.drawString(1, 2 * 12, "Pulse Length: ");
    display.drawString(16 * charPosition, 2 * 12, String(pulseLength));
    display.drawString(1, 3 * 12, "Ready to Fire!");

    break;
  case 2:
    display.drawString(1, 1 * 12, "Nozzle No: ");
    display.drawString(13 * charPosition, 1 * 12, String(nozzleNumber));
    display.drawString(10, 2 * 12, "Pulse Length: ");
    display.drawString(16 * charPosition, 2 * 12, String(pulseLength));
    display.drawString(1, 3 * 12, "Ready to Fire!");
    break;
  case 3:
    display.drawString(1, 1 * 12, "Nozzle No: ");
    display.drawString(13 * charPosition, 1 * 12, String(nozzleNumber));
    display.drawString(1, 2 * 12, "Pulse Length: ");
    display.drawString(16 * charPosition, 2 * 12, String(pulseLength));
    display.drawString(10, 3 * 12, "Ready to Fire!");
    break;
  default:
    display.drawString(0, 55, "Menu Error!");
    break;
  }
  display.display();

  /*
  if (digitalRead(bootPin) == LOW)
  {
    // testing out the Boot button switch
    Serial.println("Boot Switch pressed!");
    ledMode = !ledMode;
    digitalWrite(PowerLEDPin, ledMode);
    SoundBuzzer();
  }
  if (digitalRead(userSWPin) == LOW)
  {
    // testing out the User button switch
    Serial.println("User Button pressed");
    ledMode = !ledMode;
    digitalWrite(PowerLEDPin, ledMode);
    SoundBuzzer();
  }
  */
  delay(1000);
}

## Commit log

2022-03-18 initial import of Controller and Driver PCB KiCAD 5.1 designs
    [Power.sch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]
2022-03-22 final PCB KiCAD design files for V0.5 as sent off for manufacture at JLCPCB 2022-03-22
    [Power.sch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]
2022-03-27 Adding in the Gen3.1 printhead KiCAD PCB design files
    [Nozzle-chamber.step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]
2022-03-27 adding in Printhead schematic diagram
2022-03-29 adding in Gen3.1a Conector PCB inlet modifications - hole reduced from 1.27mm to 1mm, or 0.8mm
    [Nozzle-B_Cu.gbl, Nozzle-B_Mask.gbs, Nozzle-B_SilkS.gbo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]
2022-03-29 updated Printhead to Gen3.1b - Nozzle screw holes swapped from 1.27mm to 0.635mm. Added labels to each board to help with identification
    [Nozzle-B_Cu.gbl, Nozzle-B_Mask.gbs, Nozzle-B_SilkS.gbo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]
2022-04-03 Repo now has an updated panel with 3mm holes in top plate. Each layer is alphabet coded.
    [Nozzle-B_Cu.gbl, Nozzle-B_Mask.gbs, Nozzle-B_SilkS.gbo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]
2022-04-26 Adding in PCB testing software
2022-04-26 adding PCB stencil files and updated BOM listings that include LCSC part nnumbers
    [Printhead-Controller_bom_0.5c1.xlsx, Printhead-Driver_bom_0.5c1a.xlsx]
2022-05-11 Updating Controller and Driver boards to version 0.6
    [Printhead-Controller-B_Cu.gbl, Printhead-Controller-B_Mask.gbs, Printhead-Controller-B_SilkS.gbo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]
2022-05-11 adding in ESP32 DAC to ADC121 check/test
2022-05-12 Updated BOM spreadsheets with LCSC partnumbers. Changed schematic and voltage divider values
    [Printhead-Controller_bom_0.6a.xlsx, Printhead-Driver_bom_0.6a.xlsx]
2022-06-10 adding in test code of V0.6 PCB
2022-06-11 fixes for VSW voltage readings
    [main.cpp]
2022-06-14 Adding in version 0.7 KiACD design files
    [Power.sch, Printhead-Controller.kicad_pcb, Printhead-Controller.sch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]
2022-06-14 changes to make Rotary Encoder work better. Still configured for VSW monitoring
2023-02-08 added fusion archive files
    Added the complete base design files from fusion 360 and eaglePCB to allow editing and modification of the underlying design.
    [opjpcbprintheadassemblyv5 v14.step, opjpcbprintheadassemblyv5 v15.f3z]
